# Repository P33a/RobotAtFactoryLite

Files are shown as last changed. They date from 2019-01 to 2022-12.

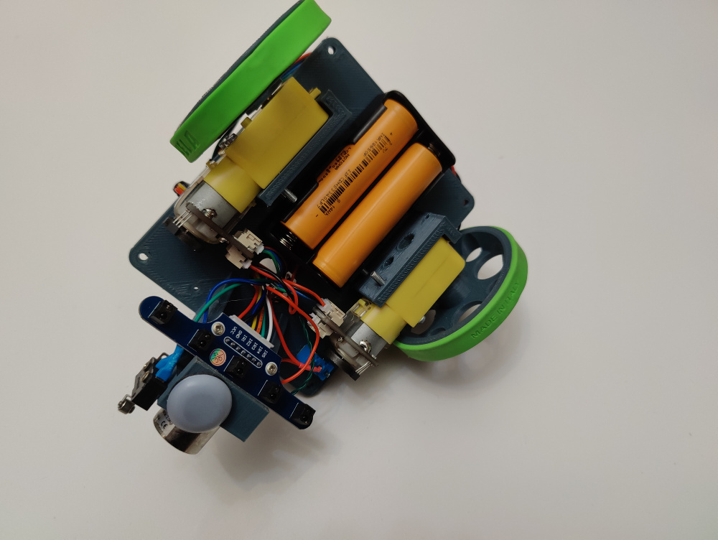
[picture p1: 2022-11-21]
robot2023/Robot2023c.jpg

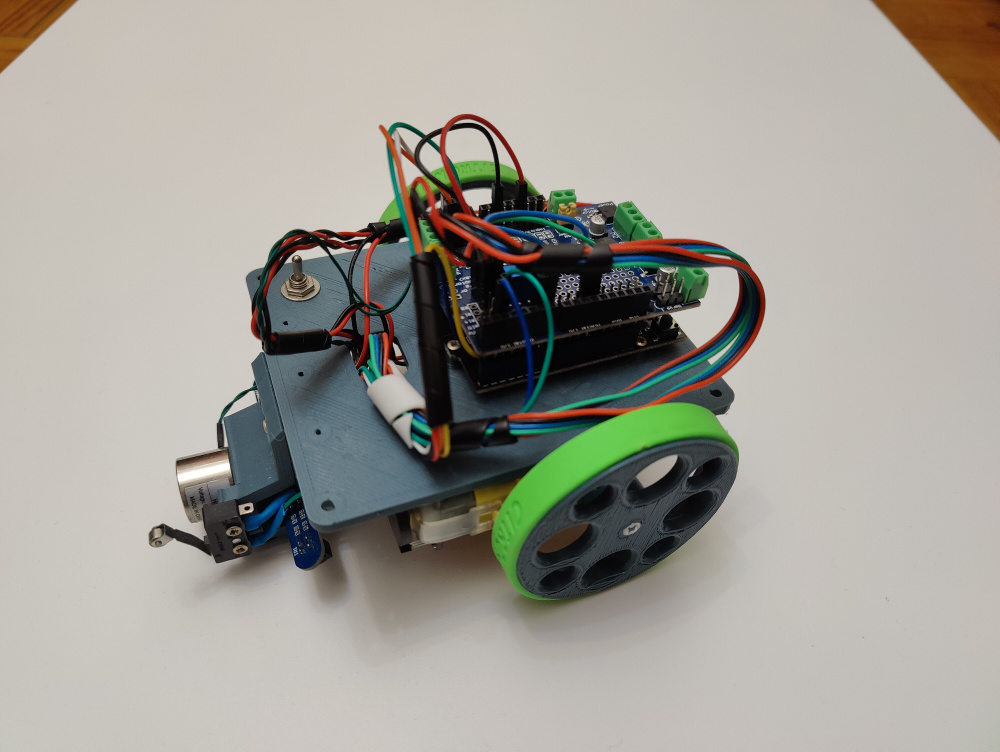
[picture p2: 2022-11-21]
robot2023/Robot2023b.jpg

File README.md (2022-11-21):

# RobotAtFactoryLite
Robot at Factory Lite Competition files:

 - Rules

 - Layout (svg and pdf)

 - Printable Sample Box

 - Printable Robot Prototypes: 
   - Stl Files
   - Arduino Demo Code <a href="https://github.com/P33a/SimTwo/tree/master/RobotFactoryLite2022/rafliteduinoHWLoopESP" target="_blank">here</a>

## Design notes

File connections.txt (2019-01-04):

RFID

13 - SCK
12 - MISO
11 - MOSI

8  - RST
7  - SDA(SS)

NC   - IRQ
GND  - GND
3.3v - 3.3v

IRSensor

A0 - IR5
A1 - IR4
A2 - IR3
A3 - IR2
A4 - IR1

GND - GND
5v  - VCC

A5 - VBat/Shutdown

Motores 
A - Left Motor
B - Right Motor
A/B1 = 1, A/B2 = 0 -> Forward
A/B1 = 0, A/B2 = 1 -> Backward

9 - PWMA
6 - AIN1
5 - AIN2

10 - PWMB
4 - BIN1
3 - BIN2

Solenoid

2 - Sol_In

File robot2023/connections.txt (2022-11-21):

Right Motor -> M1
Left  Motor -> M2

#define ENC1_A 27  (Uno 6) // Green
#define ENC1_B 14  (Uno 7) // Blue

#define ENC2_A 19  (Uno 11) // Blue
#define ENC2_B 23  (Uno 12) // Green 

int analog_pins[5] = {33, 32, 39, 36, 34};

Blue   IR1 IO33
Yellow IR2 IO32
Orange IR3 IO39
Green  IR4 IO36
White  IR5 IO34

#define TOUCHSW 12

M1              M2
Black Red       Black Red

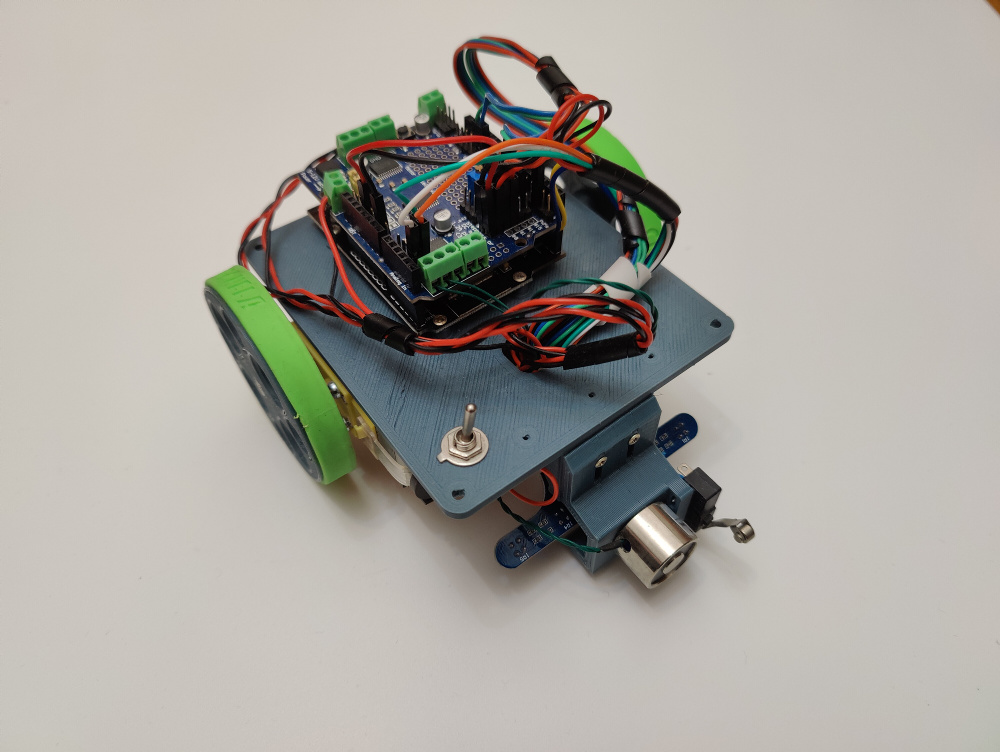
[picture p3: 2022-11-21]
robot2023/Robot2023a.jpg

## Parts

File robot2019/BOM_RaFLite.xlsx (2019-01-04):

Robot@Factory Lite
Suggested components
Component | Botnroll | PTRobotics
Motor + wheel (2x) | https://www.botnroll.com/en/dc-motor/2975-hobby-gearmotor-200rpm-65mm-wheel.html | https://www.ptrobotics.com/rodas/6345-rubber-wheel-w-micro-dc-geared-motor-3-6v.html
RFID Reader | https://www.botnroll.com/en/rf-lora/2580-rfid-module-rc522-kit-13-56mhz-6cm-with-tags-s50.html | https://www.ptrobotics.com/rfid/4787-rc522-rfid-starter-kit.html
Line Sensor | https://www.botnroll.com/en/infrared/2586-tracker-sensor-infrared-line-tracking.html | https://www.ptrobotics.com/opticos/1224-qtr-8a-reflectance-sensor-array.html
Magnet | https://www.botnroll.com/en/solenoides/976-grove-electromagnet.html | https://www.ptrobotics.com/solenoides-e-electroimans/4286-grove-electromagnet.html
Caster | https://www.botnroll.com/en/wheel/604-rodizio-miniatura.html | https://www.ptrobotics.com/casters/1237-ball-caster-plastic-3-8.html
Battery support | 2x https://www.botnroll.com/en/accessories/1299-support-for-1-battery-mr18650-w-wires.html | https://www.ptrobotics.com/suportes/6668-2x18650-lithium-battery-charger-w-barrel-jack-connector.html
Motors driver | https://www.botnroll.com/en/controllers/1957-adafruit-tb6612-12a-dcstepper-motor-driver-breakout-board-.html | https://www.ptrobotics.com/motor/828-tb6612fng-dual-motor-driver-carrier.html
Arduino nano | https://www.botnroll.com/en/arduino-boards/934-arduino-nano-30-compativel.html | https://www.ptrobotics.com/plataformaarduino-e-modelos-alternativos-equivalentes/5458-iteaduino-mini-nano-v30-atmega328-board-for-arduino-ide-arduino-compatib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
Arduino nano shield | https://www.botnroll.com/en/shield-prototype/2373-nano-io-shield-for-arduino-nano.html | https://www.ptrobotics.com/shields-proto-e-screw/5457-arduino-nano-io-expansion-shield-for-arduino-uno-nano-30-compatible.html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
Lithium battery | https://www.botnroll.com/en/batteries/2300-re-battery-li-ion-mr18650-37v-2550mah.html | https://www.ptrobotics.com/baterias-litium/6637-lithium-ion-polymer-re-battery-mr18650-36v-3350mah.html
Step down converter | https://www.botnroll.com/en/dcdc-converters/937-lm2596-step-down.html | https://www.ptrobotics.com/alimentacao/2647-lm2596-dc-dc-buck-converter-step-down-power-module-output-125v-35v.html
Micro switch | https://www.botnroll.com/en/switchs-buttons/2026-microswitch-with-roller-.html | https://www.ptrobotics.com/microswitch/5882-microswitch-3a-roller.html
Connection Wires | https://www.botnroll.com/en/cables/437-conjunto-de-50-fios-f-f-de-100mm.html | https://www.ptrobotics.com/jumper-wires/6483-premium-femalefemale-jumper-wires-100mm-pack-of-40.html
 | https://www.botnroll.com/en/cables/1088-jumper-wires-connected-6-mf-40-pack.html | https://www.ptrobotics.com/jumper-wires/4104-jumper-wires-connected-6-ff-pack-of-20.html
Battery Charger | https://www.botnroll.com/en/chargers/2563-battery-charger-4-slots-18650-3-7v-with-eu-plug.html | https://www.ptrobotics.com/carregadores/5932-2x18650-lithium-battery-charger.html

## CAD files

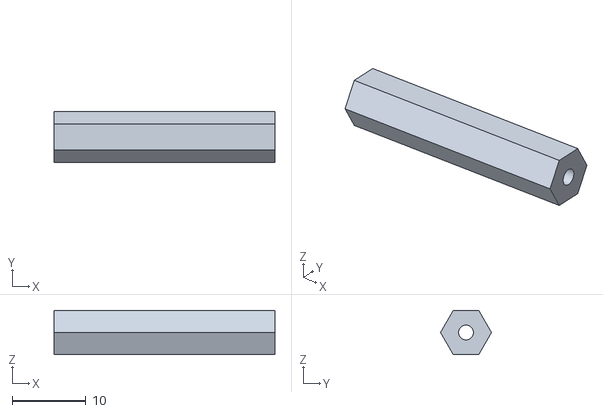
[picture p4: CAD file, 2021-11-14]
robot2019/pillar.stl
30.0 x 6.93 x 6.00

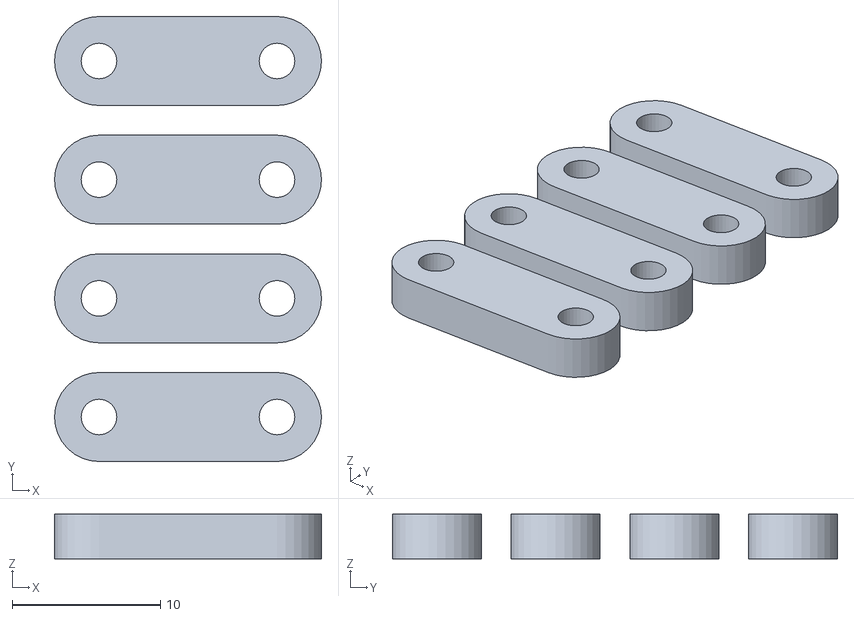
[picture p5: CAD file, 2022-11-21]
robot2022/hinge.stl
18.0 x 30.0 x 3.00

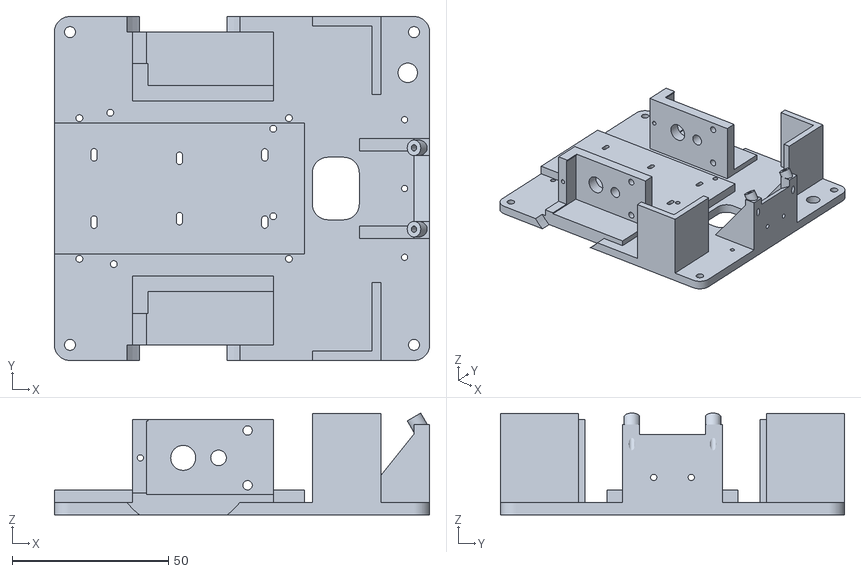
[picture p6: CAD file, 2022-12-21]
robot2023/raft_bot_v3b.stl
120.0 x 110.0 x 32.6

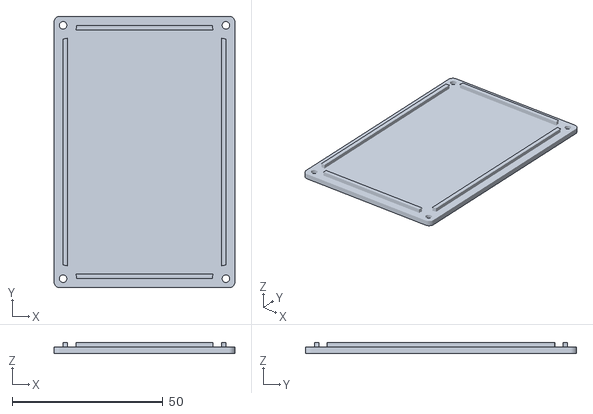
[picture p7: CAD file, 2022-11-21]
SimpleCase - Lid only.stl
60.0 x 90.0 x 3.50

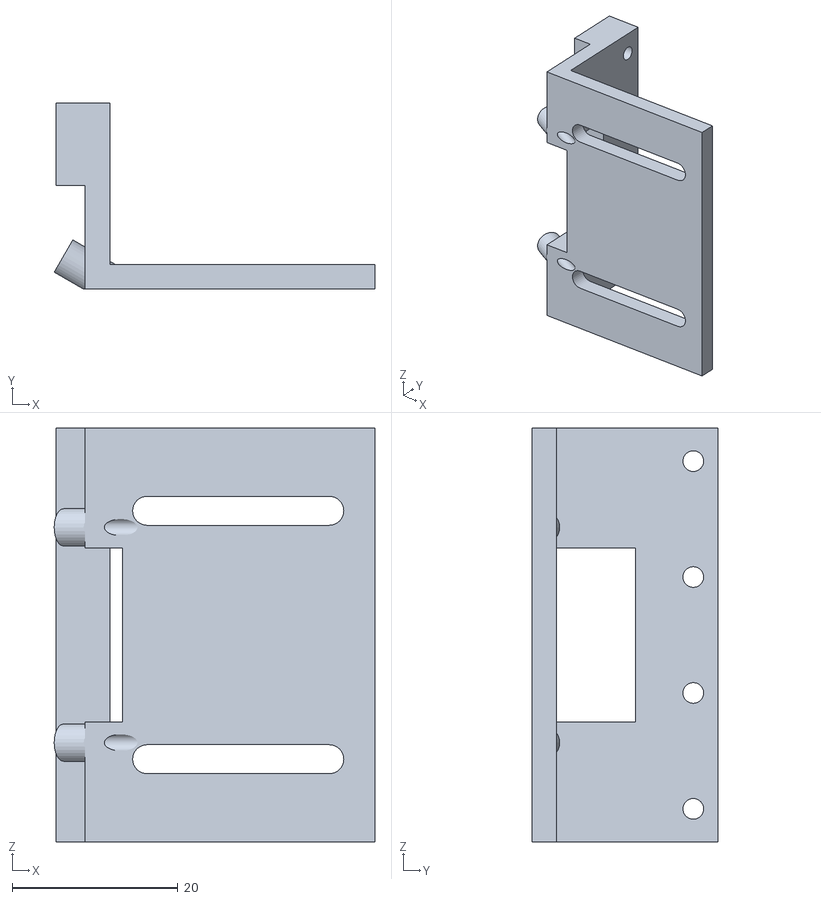
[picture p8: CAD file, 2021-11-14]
robot2019/raflite_RFID_support.stl
38.7 x 22.5 x 50.0

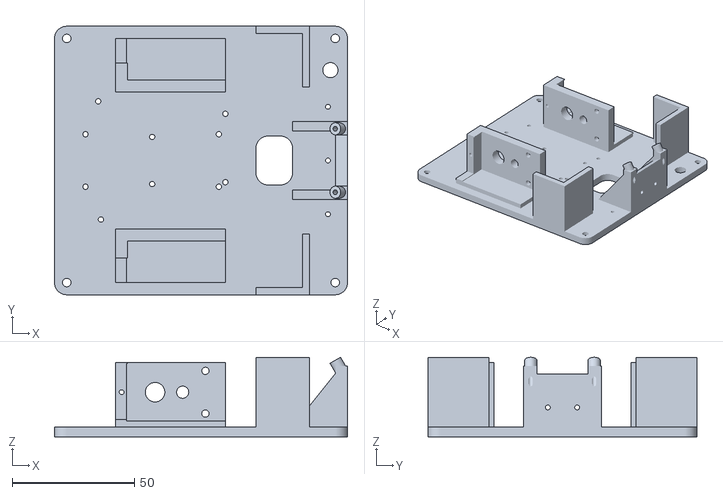
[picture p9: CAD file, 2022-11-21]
robot2022/raft_bot_v3.stl
120.0 x 110.0 x 32.6

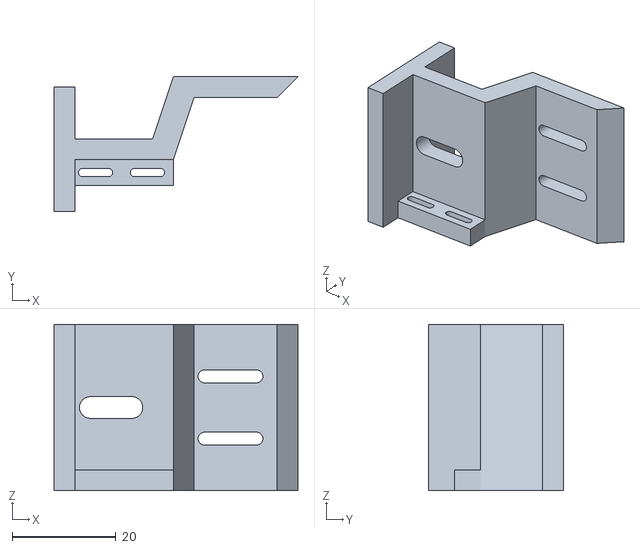
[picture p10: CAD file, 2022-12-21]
robot2023/ratf_solenoid_v3.stl
47.0 x 26.0 x 32.0

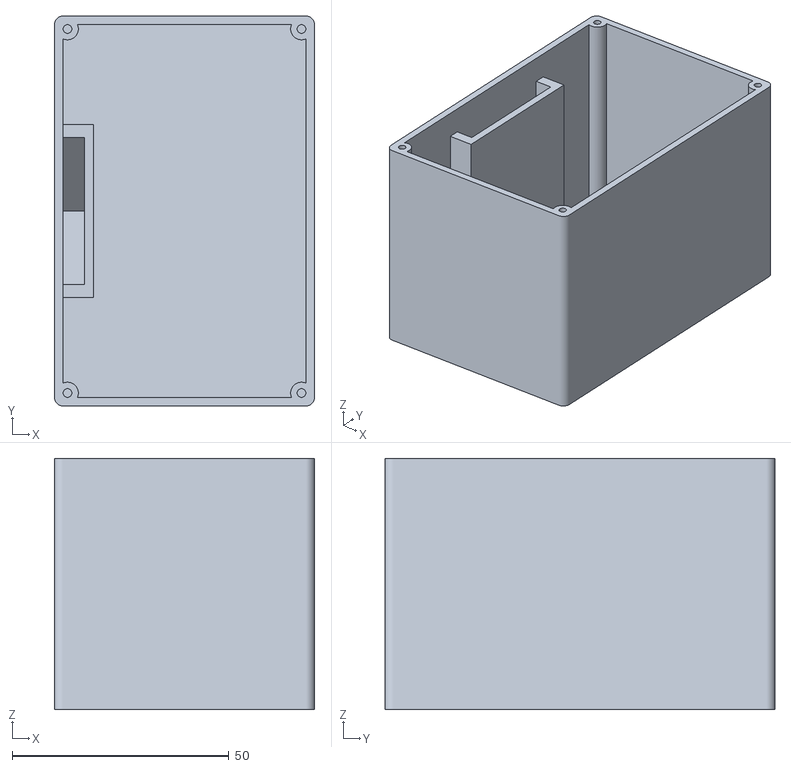
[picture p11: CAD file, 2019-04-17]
SimpleCase - Case only.stl
60.0 x 90.0 x 58.0

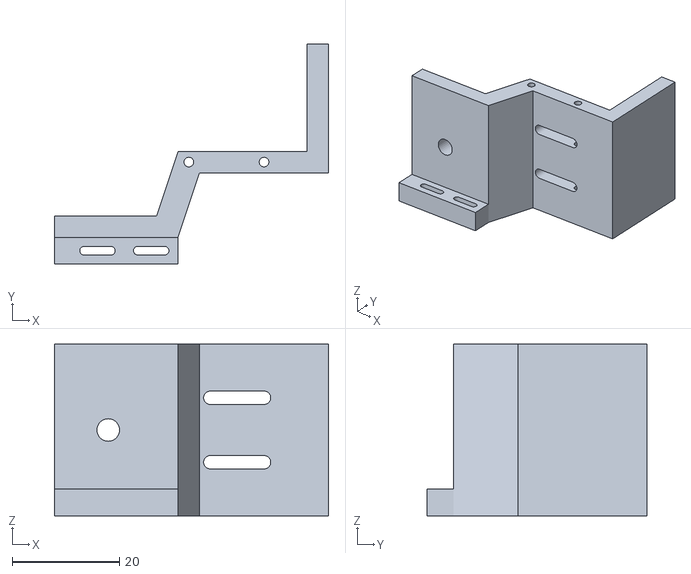
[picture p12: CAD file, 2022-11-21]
robot2022/ratf_solenoid_v2.stl
51.0 x 41.0 x 32.0

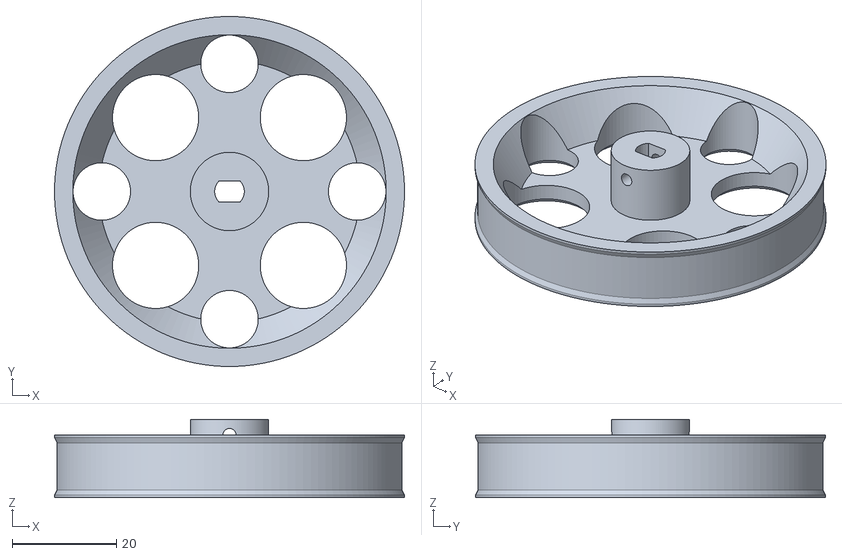
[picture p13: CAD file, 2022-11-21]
robot2023/yellow_motor_wheel_bearing.stl
67.0 x 67.0 x 15.0

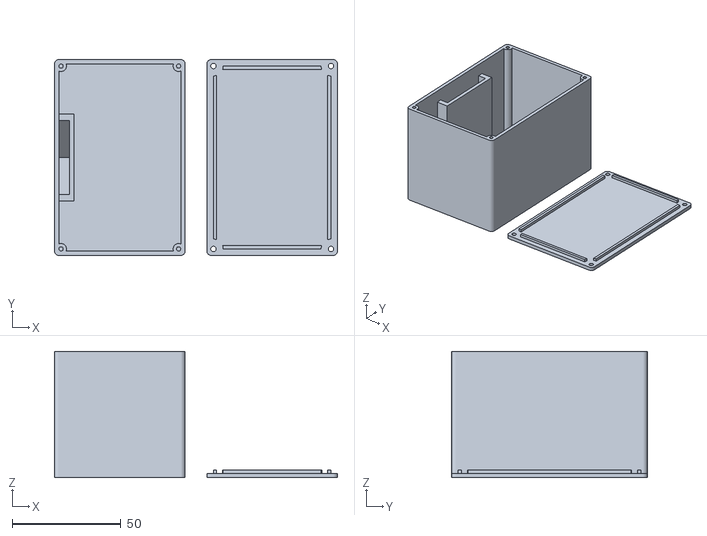
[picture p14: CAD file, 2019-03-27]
SimpleCase.stl
130.0 x 90.0 x 58.0

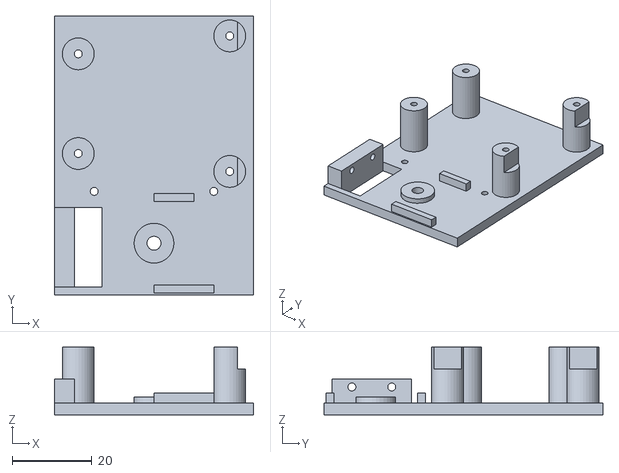
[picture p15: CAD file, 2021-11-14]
robot2019/raflite_RFID.stl
50.0 x 70.0 x 17.0

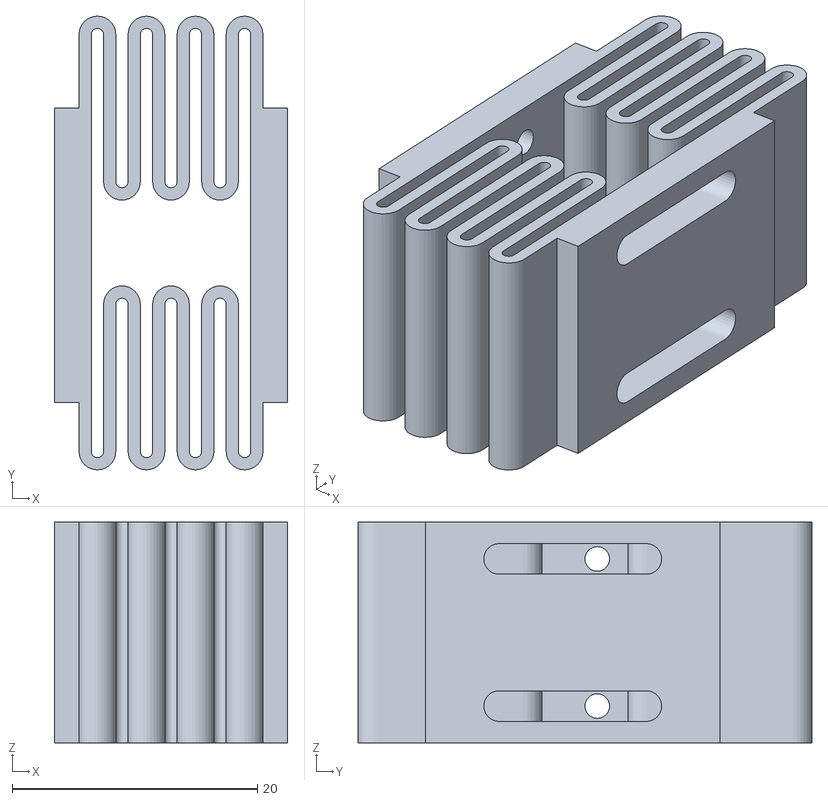
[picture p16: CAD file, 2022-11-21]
robot2022/spring_adapter.stl
19.0 x 37.0 x 18.0

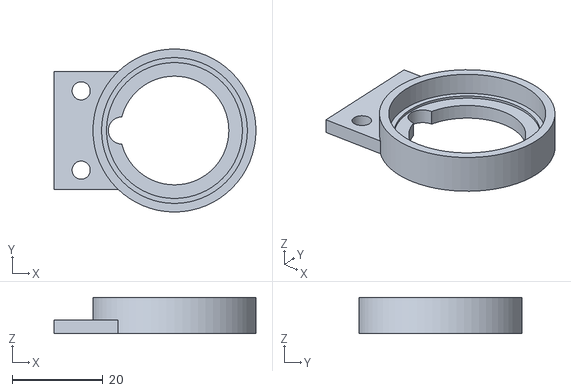
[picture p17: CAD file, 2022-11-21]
robot2023/yellow_motor_bearing.stl
44.6 x 36.0 x 8.00

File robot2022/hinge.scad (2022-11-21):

module front_guide() {
  $fn = 32;
  eps = 0.2;
  wall = 1;
  di = 2 + 2 + 2;
  difference() {
    hull() {
      translate([di, 0, 0])
      cylinder(d = 6, h = 3, center = true);

      translate([-di, 0, ])
      cylinder(d = 6, h = 3, center = true);
    }
    
    translate([di, 0, 0])
    cylinder(d = 2.4, h = 20, center = true);

    translate([-di, 0, ])
    cylinder(d = 2.4, h = 20, center = true);
  }
}

disp = 8;
front_guide();

translate([0, disp, 0])
front_guide();

translate([0, 2*disp, 0])
front_guide();

translate([0, 3*disp, 0])
front_guide();

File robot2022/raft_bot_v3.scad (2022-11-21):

//use <solenoid_support.scad>

base_h = 4;
base_len = 120;
base_width = 110;

corner_r = 5;

front = base_len/2;
back = -base_len/2;

left = base_width/2;
right = -base_width/2;

module place_things(pos_list) {
   for (t = pos_list) {  
     translate(t)
     children([0:1:$children-1]);
   }
}

pillar_holes = [
  [front - corner_r, left - corner_r], 
  [front - corner_r, right + corner_r], 
  [back + corner_r, left - corner_r], 
  //[back + corner_r - 2, 0], 
  [back + corner_r, right + corner_r]

];

center_arduino_x = 16.0;
center_arduino_y = -24.18;

arduino_holes = [
  [center_arduino_x + 0, center_arduino_y + 0],
  [center_arduino_x + 1.1, center_arduino_y + 48.4],
  [center_arduino_x -51, center_arduino_y + 15.3],
  [center_arduino_x -51, center_arduino_y + 43.3]
];


ball_holes = [
  [0 ,-16/2],
  [0 , 0],
  [0,  16/2]
];

module round_base(bl, bw, bh, cr) {
  c_x = bl / 2 - cr;
  c_y = bw / 2 - cr;
  corners = [
  [  c_x,  c_y],
  [  c_x, -c_y],
  [ -c_x,  c_y],
  [ -c_x, -c_y]
  ];  
  
  linear_extrude(height = bh, center = true, convexity = 10, $fn = 8) 
  hull() {
    place_things(corners)   
      circle(r = cr, $fn = 64); 
    }

}

extra_x = front - 8;
extra_y = 22;
extra_sensor_holes = [
  [ extra_x, -2 * extra_y/2],
  [ extra_x, 0],
  [ extra_x,  2 * extra_y/2]
];

motor_h = 22.5;
motor_wall_width = 5;
motor_wall_len = 40;

module motor_wall() {
  $fn = 32;
  difference() {
    union() {
      cube([motor_wall_len, motor_wall_width, motor_h + 2], center = true);

      translate([(motor_wall_len + motor_wall_width)/2, -7/2, 0]) 
      cube([motor_wall_width, 7 + motor_wall_width, motor_h + 2], center = true);
      
    }

    // motor support holes
    translate([motor_wall_len/2 - 31.8, 0, 17.5/2])    
    rotate([90, 0, 0])
    cylinder(d = 3, h = 20, center = true);

    translate([motor_wall_len/2 - 31.8, 0, -17.5/2])    
    rotate([90, 0, 0])
    cylinder(d = 3, h = 20, center = true);

    // motor shaft hole
    translate([motor_wall_len/2 - 11.2, 0, 0])    
    rotate([90, 0, 0])
    cylinder(d = 8, h = 20, center = true);

    // motor bump hole
    translate([motor_wall_len/2 - 22.5, 0, 0])    
    rotate([90, 0, 0])
    cylinder(d = 5, h = 20, center = true);

    // motor top hole
    translate([(motor_wall_len + motor_wall_width)/2, 0, 0])    
    rotate([90, 0, 0])
    cylinder(d = 2, h = 30, center = true);
  }
}

module motor_support() {
  motor_base_h = 3;

  difference() {
    union() {
      translate([0, 0, motor_base_h])
      motor_wall();
      
      // Motor base
      translate([motor_wall_width/2, -19/2 + 2/2, -motor_h/2 + motor_base_h/2])
      cube([motor_wall_len + motor_wall_width, motor_wall_width + 19 - 2, motor_base_h], center = true); 
    }
    // remove 0.5 from floor and front wall
    translate([0, -19/2 - motor_wall_width/2, motor_base_h])
    cube([motor_wall_len + 1, 19, motor_h + 1], center = true); 
  }
  
  // encoder protection
  disp = 43;
  translate([-disp -10, -10.5, motor_base_h/2])
  cube([3, motor_wall_width + 17, motor_h + motor_base_h + 6], center = true); 

  #translate([- disp -0.5, -23, motor_base_h/2])
  cube([motor_wall_width + 17,3,  motor_h + motor_base_h + 6], center = true); 
}

module arduino() {
  color("SteelBlue", 1)
  import("arduino_solid_holes.stl", convexity = 10);
}


module LR_bot(){
  IR_z = 25;
  $fn = 64;
  IR_wall = 5;
  IR_wall_width = 32;
  
  difference() {
    union() {
      round_base(base_len, base_width, base_h, corner_r);
      //#cube([base_len, base_width, base_h], center = true);
      
      translate([back + (30 + motor_wall_len/2), right + motor_wall_width/2 + 22, motor_h/2 + base_h/2])
      rotate([0, 0, 180])
      mirror([0, 1, 0])
      motor_support();
      
      translate([back + (30 + motor_wall_len/2), left - motor_wall_width/2 - 22, motor_h/2 + base_h/2])
      rotate([0, 0, 180])
      motor_support();
      
      //translate([10, 0, -5])
      //rotate([0, 0, 180])
      //arduino();
      

      // IR Support
      translate([front - IR_wall/2, 26/2, IR_z])
      rotate([0, -30, 0])
      cylinder(d = IR_wall, h = 5, center = false);
      // IR Support
      translate([front - IR_wall/2, -26/2, IR_z])
      rotate([0, -30, 0])
      cylinder(d = IR_wall, h = 5, center = false);
      
      translate([front - IR_wall/2, 0, IR_z/2 + base_h/2])
      cube([IR_wall, IR_wall_width, IR_z], center = true);

      // Extra support      
      translate([front - IR_wall/2, IR_wall_width/2 - 4/2, base_h/2])
      rotate([90, 0, 180])
      linear_extrude(height = 4, center = true, convexity = 10, twist = 0)
      polygon(points = [[0,0],[20,0],[0,IR_z]]);

      translate([front - IR_wall/2, -(IR_wall_width/2 - 4/2), base_h/2])
      rotate([90, 0, 180])
      linear_extrude(height = 4, center = true, convexity = 10, twist = 0)
      polygon(points = [[0,0],[20,0],[0,IR_z]]);
      
    }
    
    
    //translate([0, 0, -5])   
    //rotate([0, 0, 180])
    //arduino();
    
    translate([front - IR_wall/2, 0, 28])
    rotate([0, -30, 0])
    cube([30, 21, 10], center = true);
    
    // Solenoid holes
    translate([front - IR_wall/2, 6, 10])
    rotate([0, 90, 0])
    cylinder(d = 2, h = 10, center = true);

    translate([front - IR_wall/2, -6, 10])
    rotate([0, 90, 0])
    cylinder(d = 2, h = 10, center = true);
    
    // Switch holes
    //translate([front + 5/2 + 16, -IR_wall_width/2 + 5/2, base_h/2 + IR_z/2 + 5 + 16])
    //rotate([90, 0, 0])
    //cylinder(d = 2, h = 10, center = true);

    //#translate([front + 5/2 + 16, -IR_wall_width/2 + 5/2, base_h/2 + IR_z/2 - 5 + 16])
    //rotate([90, 0, 0])
    //cylinder(d = 2, h = 10, center = true);

    
    place_things(pillar_holes)   
    cylinder(r = 3.5/2, h = 2 * base_h, center = true);
    
    translate([back + 35, 0, 0])
    rotate([180, 0, 0])
    rotate([0, 0, 180])
    #place_things(arduino_holes)   
    cylinder(d = 2.2, h = 2 * base_h, center = true);    
    
    
    place_things(extra_sensor_holes)
    cylinder(d = 2, h = 2 * base_h, center = true); 
    
    //place_things([[40 ,0], [0, 0], [-40, -30], [-40, 30]])
    //cylinder(d = 25, h = 2 * base_h, center = true);   
    
    translate([front - IR_wall/2, 26/2, IR_z])
    rotate([0, -30, 0])
    cylinder(d = 2, h = 20, center = true);

    // IR Support hole
    translate([front - IR_wall/2, -26/2, IR_z])
    rotate([0, -30, 0])
    cylinder(d = 2, h = 20, center = true);    
    
    
    bat_x = 19.3;
    bat_y = 55.3;

    bat_x2 = 21.5;
    bat_y2 = 54.6;
    
    bat_holes = [
      [  bat_x2/2, -bat_y2/2],
      [  bat_x2/2,  bat_y2/2],
      [  bat_x/2,  0],
      [ -bat_x/2,  0],
      [ -bat_x2/2, -bat_y2/2],
      [ -bat_x2/2,  bat_y2/2] 
    ];
    
    translate([back + 76/2 + 2, 0, 0])
    rotate([0, 0, 90])
    place_things(bat_holes)
    cylinder(d = 2.2, h = 5 * base_h, center = true);   
  

    // Switch hole
    translate([front - 7, base_width/2 - 18, 0])
    cylinder(d = 6.2, h = 2 * base_h, center = true); 

    // Central hole
    translate([front - 30, 0, 0])  
    round_base(15, 20, 100, corner_r);  
  }
  
  
}



module ratf_solenoid() {
  $fn = 32;
  sw = 4;
  sh = 16;
  disp_u = 4;
  difference() {
    union() {
      linear_extrude(height = 32, center = true, convexity = 10, twist = 0)
      polygon(points = [[0, 0], 
                        [24, 0],
                        [20, sw],
                        [sw, sw],
                        [sw - disp_u, sh],
                        [-19 - disp_u, sh],
                        [-19 - disp_u, sh - sw],
                        [-disp_u, sh - sw],
                        [0, 0]
                       ]);
      
      // Switch Support
      translate([-11.5, 18.5, 13.5])
      difference() {
        cube([23, 5, 5], center = true);  
        
        hull() {
          translate([-1, 0, 0])
          rotate([0, 0, 90])
          cylinder(d = 1.6, h = 10, center = true);

          translate([-6, 0, 0])
          rotate([0, 0, 90])
          cylinder(d = 1.6, h = 10, center = true);
        }

        hull() {
          translate([9, 0, 0])
          rotate([0, 0, 90])
          cylinder(d = 1.6, h = 10, center = true);

          translate([4, 0, 0])
          rotate([0, 0, 90])
          cylinder(d = 1.6, h = 10, center = true);
        }
      }
    }    
    // center hole
    translate([-26/2, 0, 0])
    rotate([90, 0, 0])
    cylinder(d = 4.2, h = 200, center = true); 

    // body holes
    hull() {
      translate([6, 0, 12/2])
      rotate([90, 0, 0])
      cylinder(d = 2.5, h = 200, center = true); 

      translate([16, 0, 12/2])
      rotate([90, 0, 0])
      cylinder(d = 2.5, h = 200, center = true); 
    }

    hull() {
      translate([6, 0, -12/2])
      rotate([90, 0, 0])
      cylinder(d = 2.5, h = 200, center = true); 

      translate([16, 0, -12/2])
      rotate([90, 0, 0])
      cylinder(d = 2.5, h = 200, center = true); 
    }

  }
}
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

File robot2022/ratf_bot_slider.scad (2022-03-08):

module LR_bot_slider() {
  $fn = 32;
  sw = 4;
  sh = 44.5;
  difference() {
    linear_extrude(height = 26, center = true, convexity = 10, twist = 0)
    polygon(points = [[0, 0], 
                      [16, 0],
                      [16, sw],
                      [12, sw],
                      [12, sw + 4],
                      [sw, sw + 4],
                      [sw, sh],
                      [-26, sh],
                      [-26, sh - sw],
                      [0, sh - sw],
                      [0, 0]
                     ]);
    
    // center hole
    translate([-26/2, 0, 0])
    rotate([90, 0, 0])
    cylinder(d = 2.8, h = 200, center = true); 

    // body holes
    translate([8, 0, 15/2])
    rotate([90, 0, 0])
    cylinder(d = 2, h = 200, center = true); 

    translate([8, 0, -15/2])
    rotate([90, 0, 0])
    cylinder(d = 2, h = 200, center = true); 


  }
}

LR_bot_slider();

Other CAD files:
robot2019/raflite_up_short_v2.stl
robot2022/arduino_solid_holes.stl
robot2023/arduino_solid_holes.stl
robot2019/yellow_motor_support_v20.stl
robot2022/ratf_solenoid.scad
robot2019/pillar_v20.stl
robot2019/raflite_base_short_v2.stl
robot2019/raflite_base_short_v20.stl
robot2019/raflite_spacer.stl
robot2019/raflite_stepdown.stl
robot2019/slider_support.stl
robot2019/yellow_motor_support.stl
robot2022/raft_bot.scad
robot2022/raft_bot.stl
robot2022/ratf_bot_slider.stl
robot2022/ratf_solenoid.stl
robot2022/ratf_solenoid_v2.scad
robot2022/spring_adapter.scad
robot2022/uno_support.scad
robot2022/uno_support.stl
robot2022/yellow_motor_wheel.scad
robot2022/yellow_motor_wheel.stl
robot2023/raft_bot_v3b.scad
robot2023/ratf_solenoid_v3.scad
robot2023/uno_support.scad
robot2023/uno_support.stl
robot2023/yellow_motor_bearing.scad
robot2023/yellow_motor_wheel_bearing.scad

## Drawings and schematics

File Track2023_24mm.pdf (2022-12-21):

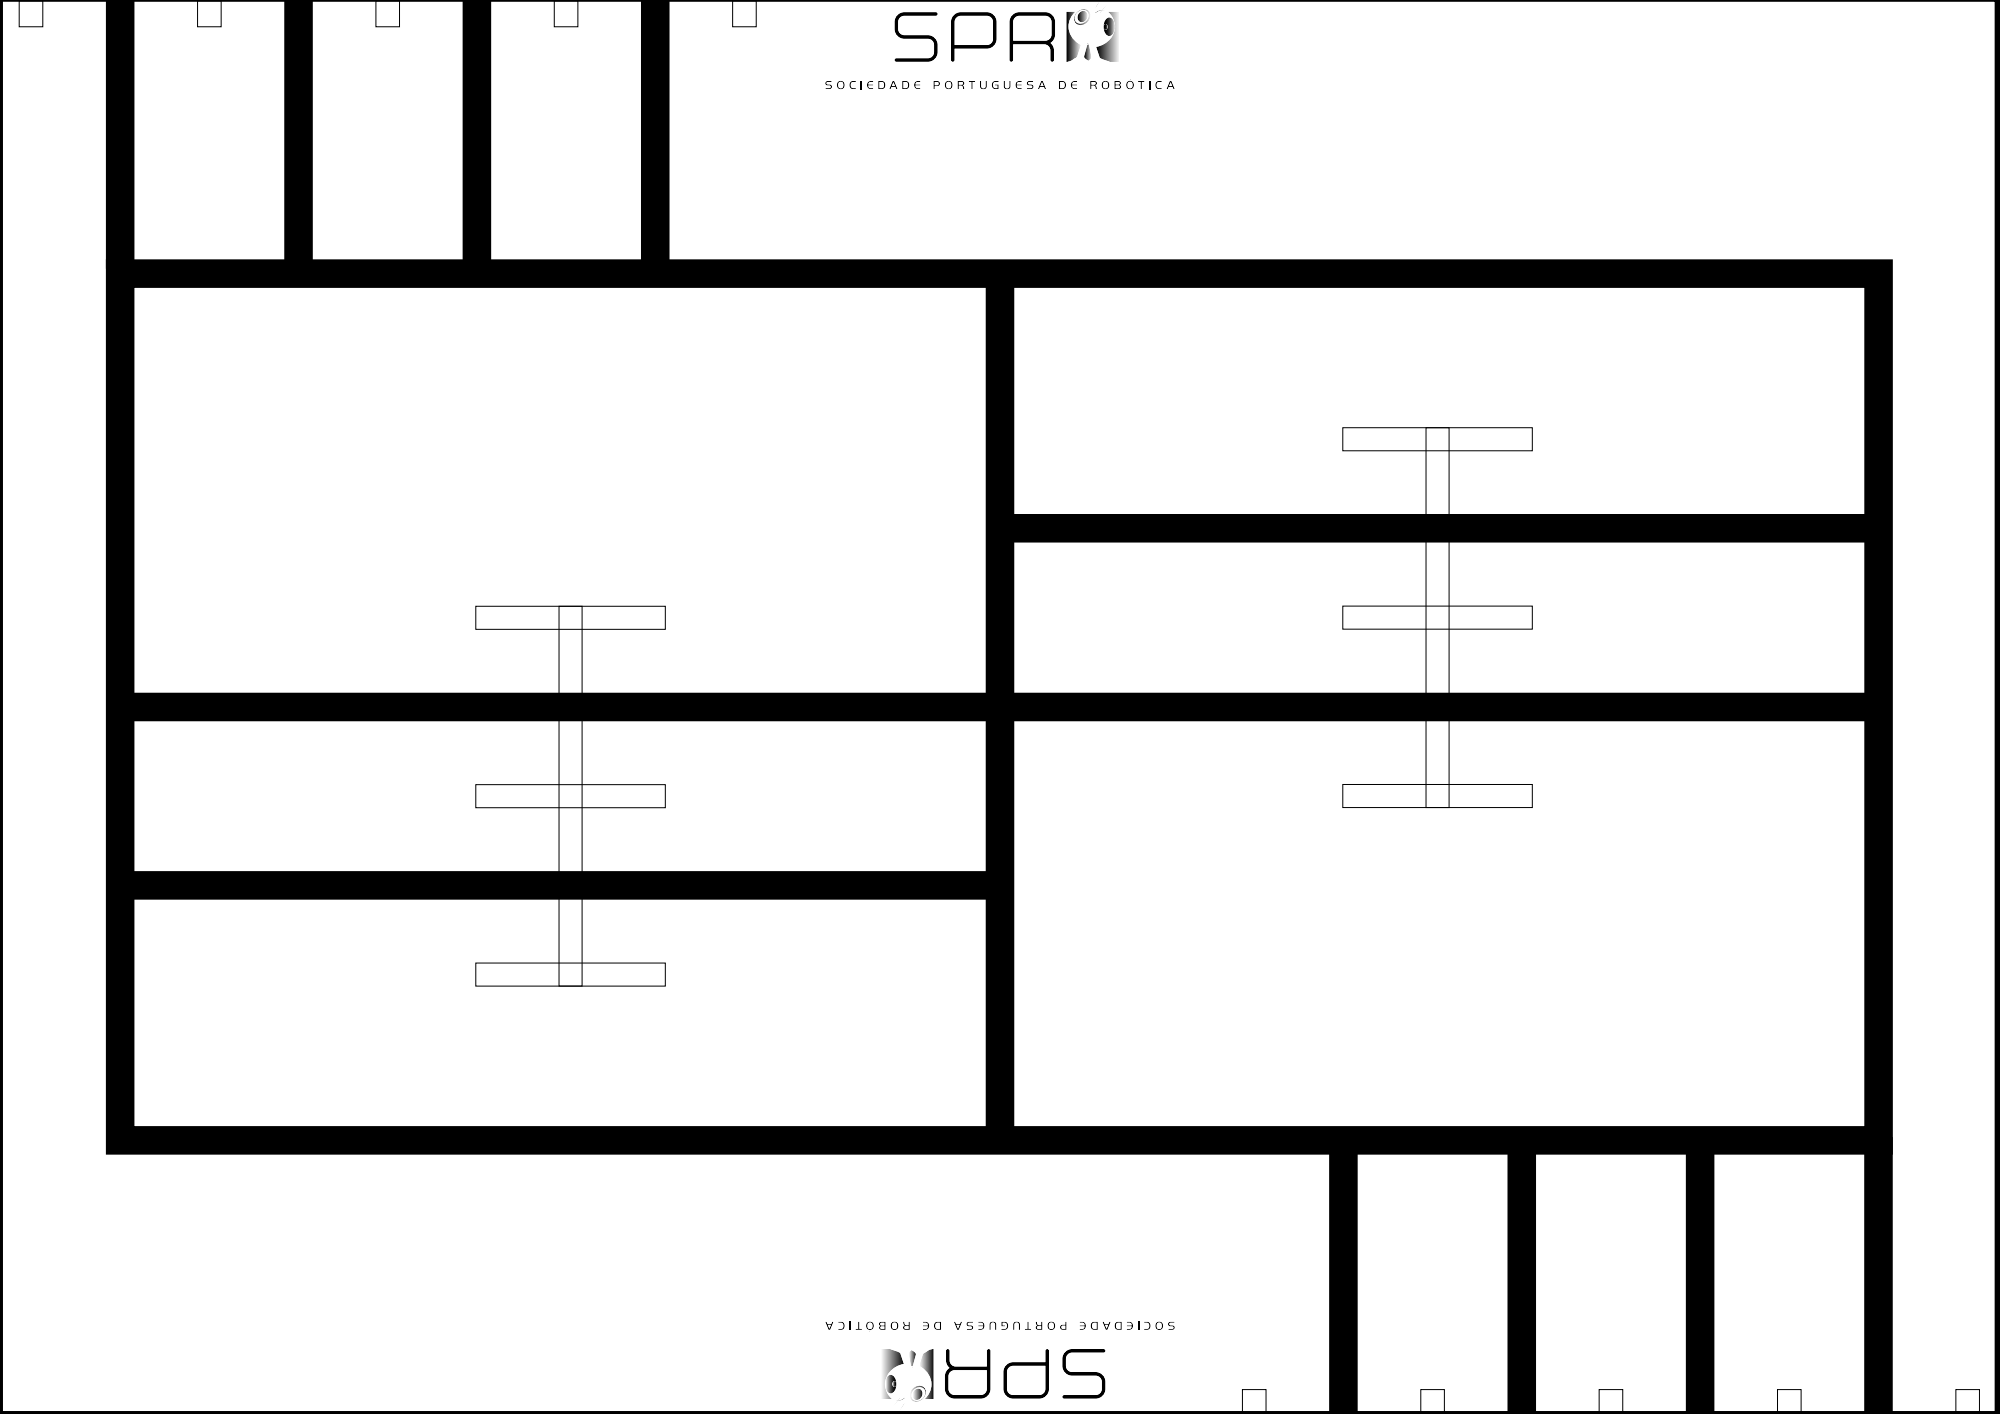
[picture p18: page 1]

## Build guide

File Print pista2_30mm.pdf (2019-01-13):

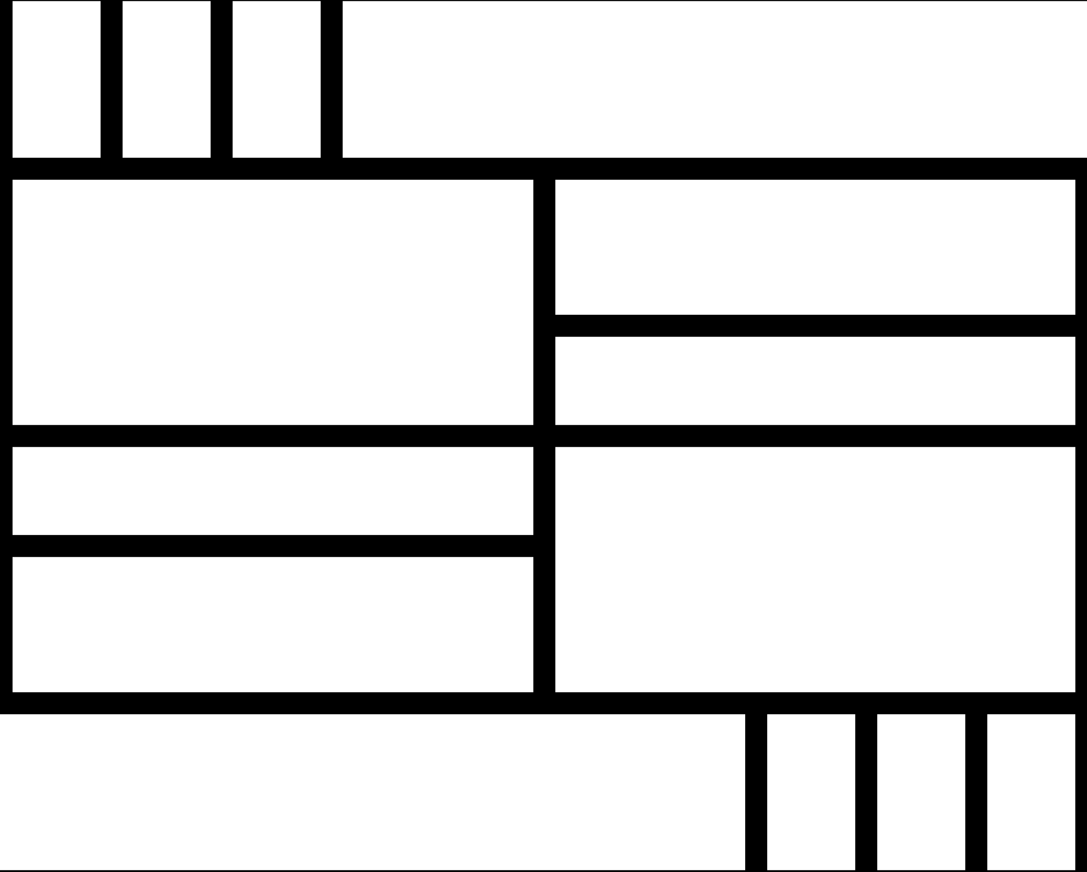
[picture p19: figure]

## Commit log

2019-01-12 Part adjusted
    [SimpleCase.stl]
2019-01-13 New Track Layout
2019-02-16 RFID Box slot made bigger
    [SimpleCase.stl]
2019-02-16 Warehouses and machines
    [raflite_wall_U.stl, raflite_wall_staple.stl, raflite_wall_top.stl]
2019-03-24 Slider support to replace Ball Caster
    [slider_support.stl]
2019-03-27 Better case lid
    [SimpleCase.stl]
2019-04-17 Case without lid
    [SimpleCase - Case only.stl]
2019-04-25 Added tag classification
    [TagsRFID.xlsx]
2019-05-07 Shorter Robot base and top
    [raflite_base_short_v2.stl, raflite_up_short_v2.stl]
2019-05-07 Remove old base
    [raflite_base.stl]
2019-10-10 Missing pillar files
    [pillar.stl, pillar_v20.stl]
2019-11-08 Encoder motor support
    [raflite_base_short_v20.stl, yellow_motor_support_v20.stl]
2021-11-14 old folders
    [BOM_RaFLite.xlsx, pillar.stl, pillar_v20.stl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]
2022-03-02 Added Robot 2022 STL files
    [raft_bot.stl, ratf_bot_slider.stl, ratf_solenoid.stl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]
2022-03-08 scad files
    [arduino_solid_holes.stl, raft_bot.scad, ratf_bot_slider.scad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]
2022-09-25 separate STL for Lid
    [SimpleCase - Lid only.stl]
2022-11-21 Rules and Track for 2022
    [SimpleCase - Lid only.stl, TagsRFID.xlsx, arduino_solid_holes.stl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]
2022-12-21 Add SPR Logo
    [raft_bot_v3b.scad, raft_bot_v3b.stl, ratf_solenoid_v3.scad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]
